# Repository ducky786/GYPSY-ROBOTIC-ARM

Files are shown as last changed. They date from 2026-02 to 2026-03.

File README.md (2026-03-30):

### GYPSY

### What is Gypsy?
Gypsy is a 5-axis robotic arm powered by an ESP32. It uses 2 20kg servos, an MG99S servo, and an MG90 servo for simplicity, torque, and affordability. It stands around a foot tall with the ability to be controlled by an Xbox controller. All parts are 3D printed to allow future modifications and easy maintenance.

### How to control the arm?
To use the Robotic arm, first plug in the power to the ESP32 and the servo motor controller. Next, take your Bluetooth Xbox controller switch into pairing mode. Using the BluePad32 library, the controller and the ESP32 should automatically pair. After the controller has paired, you can click X to move the arm into a homed position. Using the Left joystick, you can move the end effector up and down. Using the right joystick, you can move the end effector left, right, front, and back. Finally, using the left and right bumpers, you can open and close the end effector.

### Why I decided to make GYPSY?
I decided to make gypsy because of my love for robotics! I have just recently gotten into this wonderful field of engineering and wanted to expand my knowledge. Through Hack Club's grant programs, I have created RC cars and macropads, where I learned a lot! But now I wanna learn more advanced concepts such as Inverse Kinematics, CAD designing. I built Gypsy as a project where I could learn these advanced concepts and apply them to the arm. I later even hope to add object detection using OpenCV.





### Robotic Arm:


### Wiring Diagram:


### Fabrication:
For testing, I fabricated the gripper, as it is the only part that I could put together and test with the things I have right now! 
I got this 3D printed with the help of my FRC team! They kindly allowed me to borrow their prusa mini to print out the parts.

Everything here fits together seamlessly. The only thing I might need to add is a piece of foam or something to allow the gripper to gain more grip.



[video of it working](https://blueprint.hackclub.com/user-attachments/blobs/proxy/eyJfcmFpbHMiOnsiZGF0YSI6OTIxNzMsInB1ciI6ImJsb2JfaWQifX0=--30f1914dca1a4efa6c7e6b12479e9b36fba33f8f/IMG_30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)

### Programing

I was originally worried about how I might get the Inverse kinamatics to work but I acctually came across this very easy to use IK library that does all the hard mathmatical calculations!
I first create a link of all the joints that my arm has. This includes the base, arm, foarm, and the writst. From then use these joints to in a method called solveIK which takes the the x, y and z coordinates and returns the degrees for the servo. very simple!



[IK Library:](https://github.com/cgxeiji/CGx-InverseK/tree/master)

### BOM:

| Part | Quantity  | Price  | Link |
|---|---|---|---|
| MG996R Servo | 1(4 pack) | $16.99 | https://www.amazon.com/4-Pack-MG996R-Torque-Digital-Helicopter/dp/B07MFK266B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 |
| 20KG Servo | 2 | $27.98 | [Amazon.com: LewanSoul 20KG RC Servo High Torque Servo Motors, Waterproof Full Metal Gear Steering Servo for 1/6 1/8 1/10 1/12 RC Car Robot DIY, Digital Servo with 25T Servo Horn, Control Angle 270° : Toys & Games  ](https://www.amazon.com/Torque-Waterproof-Steering-Digital-Control/dp/B073F92G2S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) |
| Servo Driver | 1 | 5.99 | [Amazon.com: Dorhea PCA9685 16 Channel 12 Bit PWM Servo Driver Board IIC Interface PCA9685 Module Controller Compatible with Raspberry Pi : Toys & Games](https://www.amazon.com/Torque-Waterproof-Steering-Digital-Control/dp/B073F92G2S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) |
| ESP 32 | 1 | 9.99 | [Amazon.com: HiLetgo ESP-WROOM-32 ESP32 ESP-32S Development Board 2.4GHz Dual-Mode WiFi + Bluetooth Dual Cores Microcontroller Processor Integrated with Antenna RF AMP Filter AP STA for Arduino IDE : Electronics  ](https://www.amazon.com/HiLetgo-ESP-WROOM-32-Development-Microcontroller-Integrated/dp/B0718T232Z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) |
| ESP Break out Board | 1 | 6.99 | [Amazon.com: Alinan 2pcs ESP32 Breakout Board GPIO 1 into 2 Compatible with 38PIN Narrow Version ESP-WROOM-32 ESP32 Microcontroller Development Board : Electronics ](https://www.amazon.com/Alinan-Compatible-ESP-WROOM-32-Microcontroller-Development/dp/B0B1HN7ZPC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) |
|3D printed parts | --| $10| --- |
|Shipping | --| $10| --- |
| Total | | $87.94 | |

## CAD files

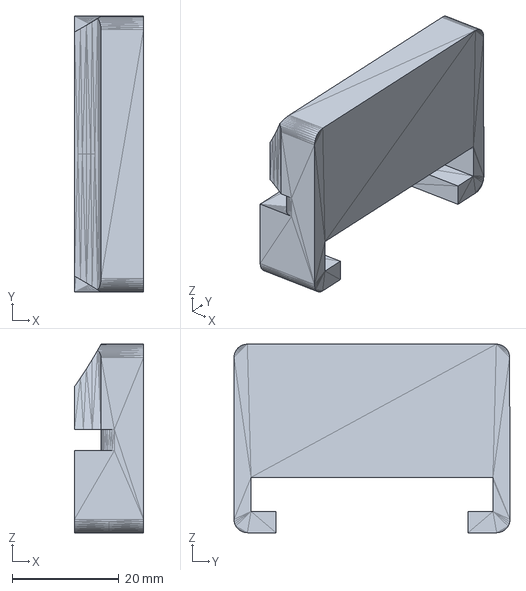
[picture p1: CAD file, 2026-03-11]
CAD/AnyConv.com__End Effector.step
13.0 x 51.8 x 35.4 mm

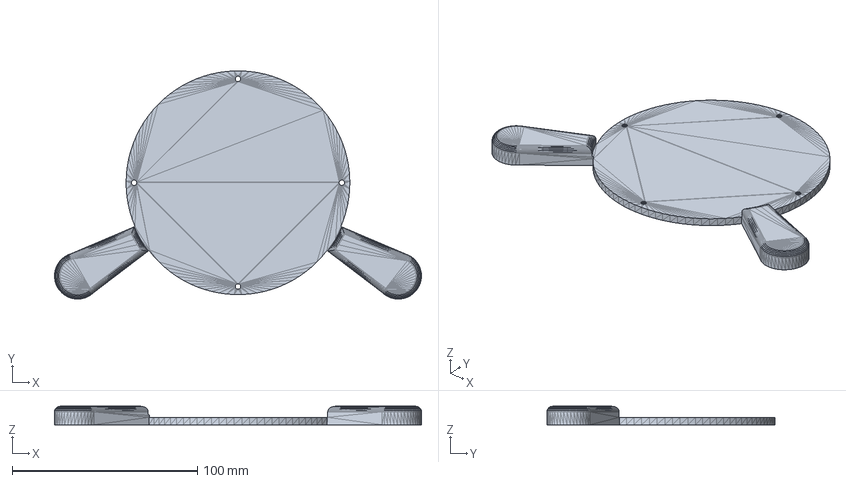
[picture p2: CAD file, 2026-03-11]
CAD/AnyConv.com__Base bottom cover.step
197.9 x 123.0 x 10.0 mm

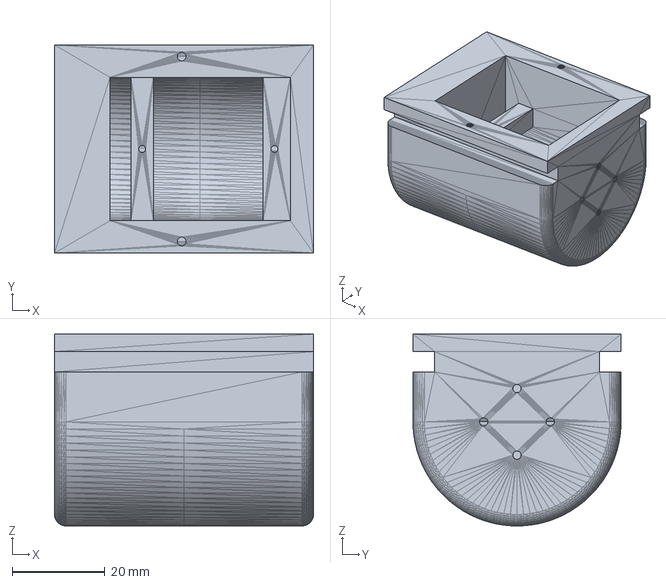
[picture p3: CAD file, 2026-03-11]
CAD/AnyConv.com__Wrist.step
56.0 x 45.0 x 41.5 mm

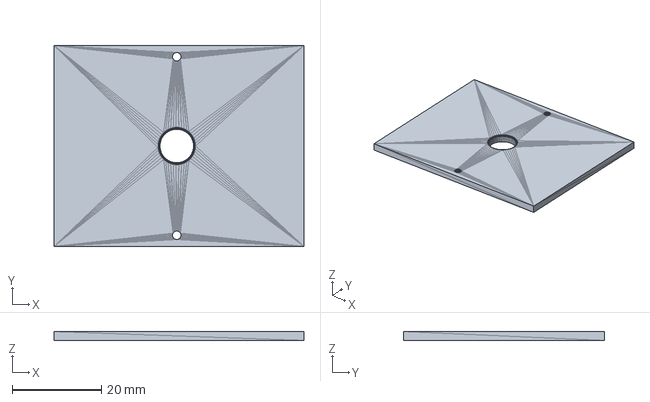
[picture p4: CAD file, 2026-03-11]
CAD/AnyConv.com__Wrist Cover.step
56.0 x 45.0 x 2.00 mm

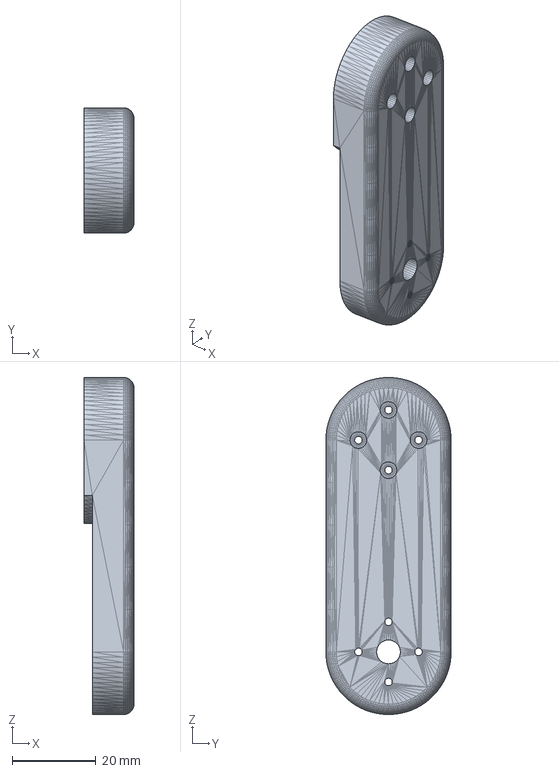
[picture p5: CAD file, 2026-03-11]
CAD/AnyConv.com__Wrist Joint.step
12.0 x 30.0 x 80.7 mm

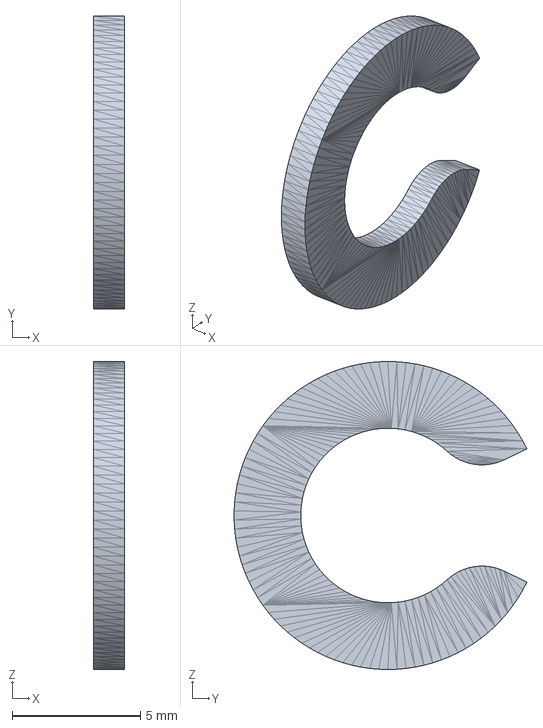
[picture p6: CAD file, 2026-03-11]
CAD/AnyConv.com__C-clip.step
1.20 x 11.4 x 12.0 mm

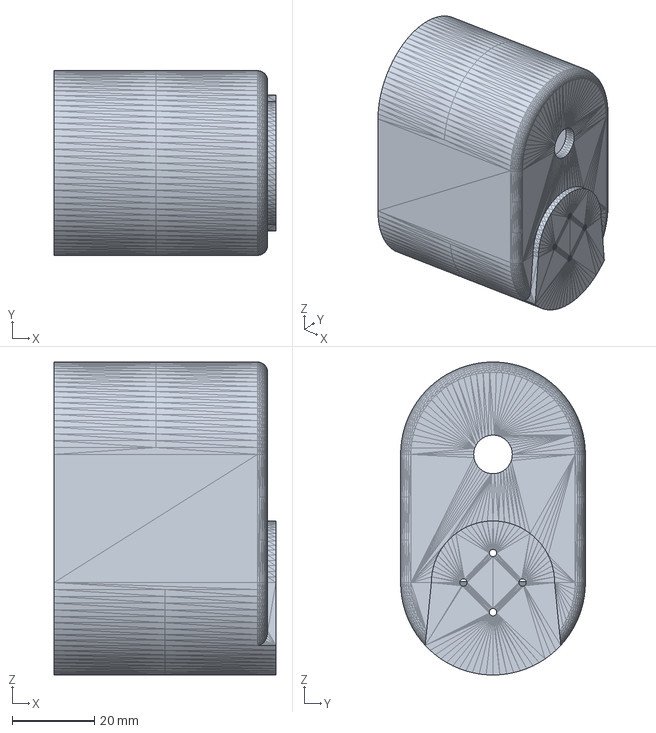
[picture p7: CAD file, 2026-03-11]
CAD/AnyConv.com__Forearm.step
54.0 x 45.0 x 76.2 mm

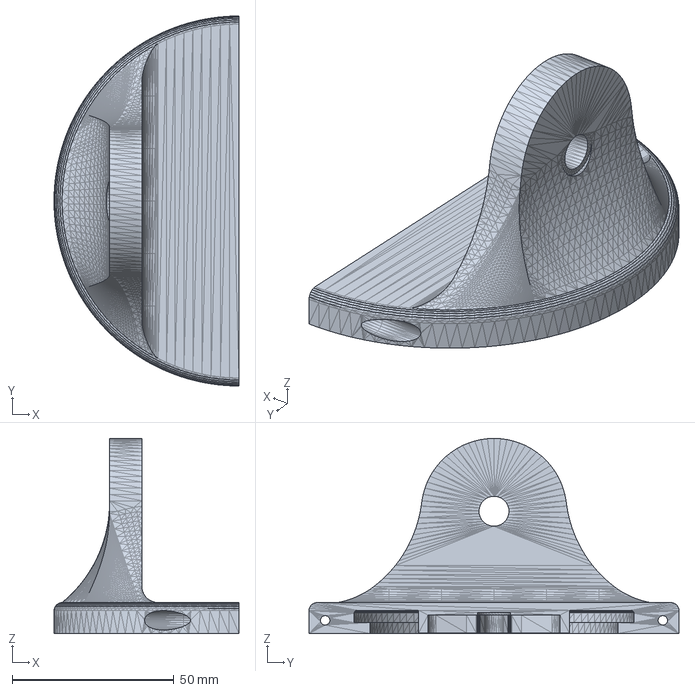
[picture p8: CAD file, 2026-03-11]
CAD/AnyConv.com__Sholder Joint.step
57.2 x 114.3 x 60.3 mm

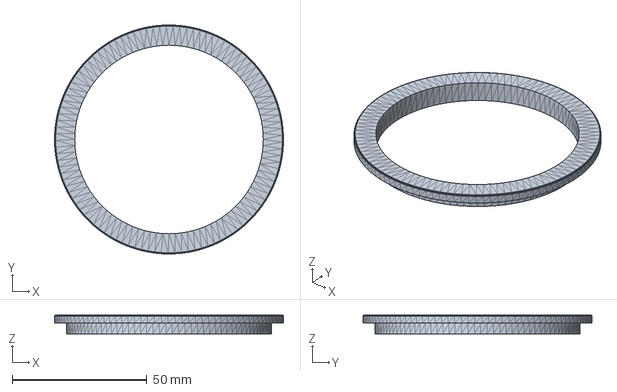
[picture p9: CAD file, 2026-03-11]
CAD/AnyConv.com__Rotation Plate.step
84.8 x 84.8 x 7.00 mm

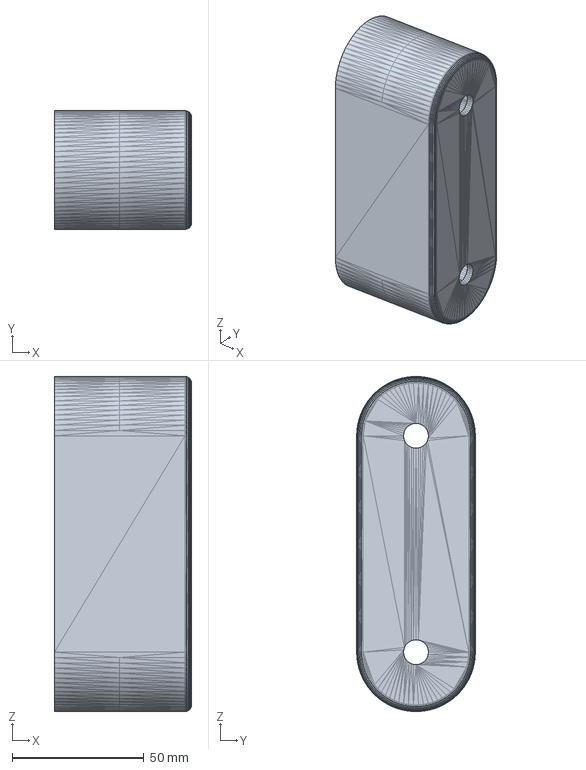
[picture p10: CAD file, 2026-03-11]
CAD/AnyConv.com__Arm.step
52.0 x 45.0 x 127.0 mm

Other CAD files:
CAD/AnyConv.com__Wrist Joint 2.step
CAD/Robotic Arm.f3z

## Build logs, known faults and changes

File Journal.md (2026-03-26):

# GYPSY-ROBOTIC-ARM
Gypsy is a 5 axis robotic arm powered by a Raspberry Pi4 small enough, to play around with on your desk.

### 1/18/26
### Research
This is my biggest project yet! I have wanted to build a robotic arm for a long time now and seeing I have gained a lot of experience from my previous projects; I am much more confident in starting this big one! I feel that I would end up learning a ton on CAD and Coding. This is my passion project! 

For this project I want to make sure It stays cheap as possible! Robotic arms are kind of expensive, and they are a great way of learning key robotics concepts like inverse kinematics (which I hope to learn). So I hope to keep this project cheap as possible for anyone who might wanna try building this!

At the start of the project, I originally wanted to create 6 axis robotic arm all powered with Nema Stepper motors! But... seeing all the other robotic arm projects, I felt it would end up becoming really expensive and too complicated for my beginner level brain. So, I dumbed it down a little and settled on a 5 axis Robotic arm with servo motors. 

These axis include:
- The base Rotation
- The shoulder Rotation
- The Forearm Rotation
- The wrist Rotation
- The End effector 

For a robotic arm to work you need to know how to move the end effector to the desired point. To be able to do this you need to know Inverse Kinematics. This is essentially a way of mathematically solving the joint variables to get the perfect end effector position. In my research on this topic, I came across this lesson from Clemson University which does a great job on teaching this stuff. Math is not my strongest suit so I will be spending a lot of time learning this stuff.

[Lesson by Clemson University] (https://opentextbooks.clemson.edu/wangrobotics/chapter/inverse-kinematics/)

### CAD

I started a bit Of the CAD too! This is only my third time CADing so am still learning some stuff. Today I worked on the base of GYPSY and finished a bit of the first axis. I had to think a lot on how I might want to approach this part of the axis. I Definity did NOT want to use Barings for this project as for one it would drastically increase the price of the arm due to such large Barings and also because of the past troubles I've had with them. In my last project when I used Barings, I had unfortunate results with them because of the tolerances. I never seemed to get the fit right. So, I ditched the idea of the Barings and settled on simply having two pieces loosely fit around a notch so it could spin. Sure, it might not be the smoothest, but it will spin pretty good, hopefully.





### 1/21/26
### CAD

Today I continued to work on the CAD for GYPSY! I worked a little more on the shoulder axis and the electronics box. The shoulder joint will contain two servos, one for the shoulder itself and the other for the forearm joint. These joints will be powered by 20kg servos for the much-needed torque. The joint is connected with a circular servo horn that gets screwed into the servo and the rotating base. The side that doesn't have a servo, is connected with a rod held by a C-clip. I found using C-clips from my last project really useful as they were very simple and effective. I really spent a lot of time making sure that the servo rotation part was perfectly aligned with the rod as any miss alignment would completely mess up the pivot.

GYPSY is powered by a RPI4, so I needed to create proper housing for it, so it doesn't look really messy. The electronic Box is a simple box with screw mounts for the RPI. Nothing fancy, kept it simple! 







### 1/25/26
### CAD
For the past couple of days, I spent more time on CAD! It is safe to say the CADing is now nearing its end. After this is done, I plan on fabricating the wrist as that is the only part that I could do without receiving the grant yet! But until then I am focused on completing GYPSY's CAD and code!

### 1. Forearm
After completing a bit of the base arm, I moved up to working on my third axis, the Forearm. This axis is similar to the base arm portion of GYPSY as it contains a MG996R servo motor. This servo is also connected to the pivoting joint via a circular servo connector which screws into the joint. This joint directly pivots the wrist. Through this whole CADing prosses I contently feared that this servo would not have enough torque to pick up anything let alone hold itself up. I don't have enough space to add gearing so the only possible option if that happens is to swap the servo motors to 20kg servos as they have almost the exact servo profile as the MG996R.

### 2. Wrist and End Effecter

The while wrist pivot is powered by the servo inside the forearm. Made it this way so it has the littlest possible weight at the top. Now inside the wrist, is a MG90 servo. This servo is powers the end effector. During my research process I looked at a lot of robotic arm designs that had crazy end effectors. they contained gears and such to open and close a clamp for the end effecter. This for me, looked very complicated as it meant that I had to somehow cad custom gears and stuff for the end effector. I did not want to go that route. I eventually came across an end effecter design on YouTube that looked super simple and unique! It uses two clamps that are pulled together with a rubber band. In the middle was a servo horn and when you wanted to open the arm, the servo horn would rotate 90 degrees splitting the claps apart. And to close the servo would simply rotate back to 0 degrees and the rubber band would pull the clamps back together. I loved this design because of how easy it was and implemented it! The way this end effecter is designed, I could easily create webcam mounts for it in the future for object detection and tracking!

Credit: https://youtu.be/AIsVlgopqJc?si=-omXVJZqu1W9qJ8N



The yellow Band is the Rubber band.

### 1/26/26
### CAD
The CAD is finally done! I completed the cad by adding some last details like names and C-clip joints. The joint is a simple rod that goes through the arm rotation axis and held together with a 2 C-clips. This design worked great for my last project, so I hope it works the same now!

Today while cleaning out some of my stuff, I came across a neopixel strip from a Pico kit that I bought a while back. I instantly though that I should add this to the front, so I created a groove in the base for it be stuck on! I could imagine the different sick patters I could display with this! I can tell it's going to come out awesome!!



### FABRICATION
For my fabrication I wont be able to do too much as I do not have majority of the parts. I can however fabricate the wrist! With the help of my robotics team, they kindly allowed me to use the 3d printer for this project! So, I printed the parts out and put it together and wrote a simple loop to test it out! The wrist came out so good. The tolerance was perfect and everything fit together seamlessly. 



Here is the video clip of it working:
[IMG_3051](/user-attachments/blobs/proxy/eyJfcmFpbHMiOnsiZGF0YSI6OTIxNzMsInB1ciI6ImJsb2JfaWQifX0=--30f1914dca1a4efa6c7e6b12479e9b36fba33f8f/IMG_3051.MOV)

The grip on the wrist is fine but I think I need to add some kind of rubber or foam for the best possible grip!

After that I moved onto writing some test code for the neopixel and came up with simple patterns.



video of testing the light pattern.
[IMG_3075](/user-attachments/blobs/proxy/eyJfcmFpbHMiOnsiZGF0YSI6OTIxNzcsInB1ciI6ImJsb2JfaWQifX0=--d5ad71ac91c631e579ebd244bddf80ecedc21ad2/IMG_3075.MOV)

### MAJOR CHANGES 
Since my last post there has been a major change! Originally the brains of the robot were supposed to be a raspberry pi. But after some consideration I think that would be something the grant would not be able to provide and also that I've gone sick of Micro Python, lol! So, I scrapped the idea of a RPI for the MK 1 version of GYPSY and settled on an ESP-32. This microcontroller is honestly a pretty sweet controller! It has blue Tooth and Wi-Fi connectivity which would be great in connecting my Xbox controller! And plus, the Arduino IDE is so much better than the dead Thonny IDE. I am also pretty familiar with JAVA so the switch to C++ wasn't too bad! So, after that decision I worked on re designing the electronic compartment of GYPSY to house the ESP-32 along with the PCA965 servo driver.



### GYPSY FIRMARE!

After tinkering around with Aduino C++ and stuff I started working on the gypsy Firmware. I will be using I2C communication to control the servos. So I added the required libraries for that and added methods to control the servos. I later spent looking for an IK library that could calculate the joint angles to get to the required x, y, z coordinates. I came across this very awesome IK library that was really simple to use!

IK Library: https://github.com/cgxeiji/CGx-InverseK/tree/master 

This library creates a link of joints with constraints to which then gets passed in to a solver method along with the x, y, z coordinates. If the location is solvable it updates the diffrent servos to their angle to reach that position!



### FINALIZATION 
After all that the theoretical code and CAD are now finally complete. I final BOM comes around $68 which doesnt seem too bad. Now All I need to do I work on submitting everything for review!

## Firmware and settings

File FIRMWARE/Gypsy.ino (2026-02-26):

//#include <ESP32Servo.h>
#include <Wire.h>
#include <Adafruit_PWMServoDriver.h>
#include <InverseK.h>



// ======== Create PWM Object ======== Default I2C address (0x40)
Adafruit_PWMServoDriver PWM = Adafruit_PWMServoDriver();



// Servo Parameters
int SERVO_MIN = 150;
int SERVO_MAX = 600;


// =========== Constants =============

//Servo Channels
const int Gripper = 0;
const int Wrist = 1; // change
const int Forearm = 2; // change
const int Arm = 3; // change
const int Waist = 4; // change


// Robot Arm Lengths (dementions in MM) (including joint length)
const float FORARM_LENGTH = 81.900;
const float ARM_LENGTH = 81.997;
const float WRIST_LENGTH = 52.703;

// const float FORARM_LENGTH = 200;
// const float ARM_LENGTH = 200;
// const float WRIST_LENGTH = 200;


// =========== End Pos Coordinates =============
float x = 50.0;
float y = 50.0;
float z = 50.0;



void setup() {
  // put your setup code here, to run once:

  Serial.begin(115200);
  Wire.begin();
  PWM.begin();
  PWM.setPWMFreq(50);
  delay(500);

  // =========== SET UP INVERSE KINAMATICS LINKS ===========
  Link base, upperarm, forearm, hand;

  base.init(0, -PI, PI);
  upperarm.init(ARM_LENGTH, -PI, PI);
  forearm.init(FORARM_LENGTH, -PI, PI);
  hand.init(WRIST_LENGTH, -PI, PI);


  InverseK.attach(base, upperarm, forearm, hand);

  float a0, a1, a2, a3;

    if(InverseK.solve(150, 0, 0, a0, a1, a2, a3, b2a(90.0))){
    
    setServoAngle(Waist,a2b(a0));
    setServoAngle(Arm,a2b(a1));
    setServoAngle(Forearm,a2b(a2));
    setServoAngle(Wrist,a2b(a3));
    Serial.println("Done");
      
  }else{
    Serial.println("nu uh");
  }


}

void loop() {
  // put your main code here, to run repeatedly:
}


void setHome(){

  setServoAngle(Gripper, 0);
  setServoAngle(Wrist, 0);
  setServoAngle(Forearm, 0);
  setServoAngle(Arm, 180);
  setServoAngle(Waist, 90);

}

// Quick conversion from the Braccio angle system to radians
float b2a(float b){
  return b / 180.0 * PI - HALF_PI;
}

// Quick conversion from radians to the Braccio angle system
float a2b(float a) {
  return (a + HALF_PI) * 180 / PI;
}

// ============== Set servo angle method ==============
void setServoAngle(uint8_t channel, int angle){
  
  int pulse = map(angle, 0, 180, SERVO_MIN, SERVO_MAX);
  PWM.setPWM(channel, 0, pulse);

}
